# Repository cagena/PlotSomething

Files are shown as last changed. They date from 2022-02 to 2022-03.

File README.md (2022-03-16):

# PlotSomething

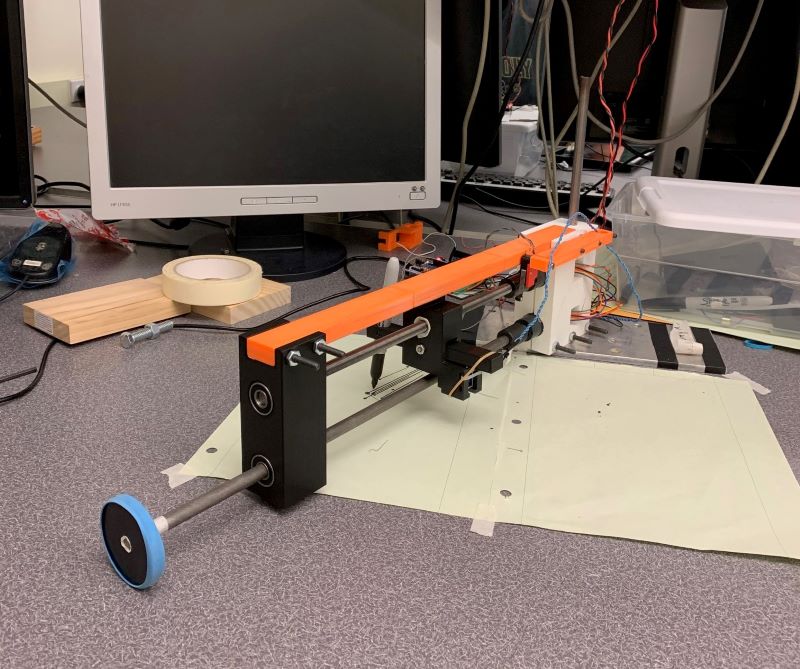
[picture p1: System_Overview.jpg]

Figure 1. System Overview

## Introduction

Our device is a pen plotter system that automatically plots an image through the use of an hpgl file. Through a serial terminal window, 
the user is initially prompted to calibrate the pen. Next, the user presses ‘p’ to plot, ‘q’ to quit, and ‘h’ to return to the welcome screen. 
After pressing ‘p’ to plot, the user is prompted to enter a hpgl filename. Once that is completed, the device will start to read the hpgl file 
and plot as the program reads each coordinate. If this filename doesn’t exist in the folder, it will prompt a message that says, 
“invalid file name”. This device is meant for people who are able to convert their desired image into an hpgl file and for those 
who want to plot something on paper without having to draw it themselves. This device is also for people who don’t want a typical, 
boring printed image on a piece of paper.

## Hardware Overview

The following table displays all of our hardware components used in this project. Fasteners such as screws, bolts, and nuts are not listed.

| Part No.  | Part |  Qty. | Source |
|:---:|:---|:-----:|:---|
| 1 | 2-in Drive Wheel | 1 | 3-D Printed |
| 2 | Track Slider/Solenoid Carrier | 1 | 3-D Printed |
| 3 | Lever Arm/Pen Carrier | 1 | 3-D Printed |
| 4 | Motor Mount | 1 | 3-D Printed |
| 5 | T-Slot Framing Rail | 1 | 3-D Printed | 
| 6 | Drive Shaft and Lead Screw Mount  | 1 | 3-D Printed |
| 7 | Limit Switch Mount | 1 | 3-D Printed | 
| 8 | Metal Base Plate | 1 | ME405 Lab |
| 9 | Base Shaft | 1 | ME405 Lab |
| 9 | 3/8 in Drive Shaft | 1 | Home Depot |
| 10 | 3/8 in-24 Threaded Rod | 1 | McMasterCarr |
| 11 | 3/8 in-24 Hex Nut | 1 | Home Depot |
| 12 | DC Voltage Limit Switch | 1 | Amazon |
| 13 | Solenoid (5V, 1.1A) | 1 | Amazon |
| 14 | Roller Bearing | 5 | Amazon |
| 15 | Set Screw Shaft Coupling | 2 | McMasterCarr |
| 16 | Black FinePoint Sharpie&trade; | 1 | Campus Bookstore  |
| 17 | Rubber Band | 2 | Home |
| 18 | Nucleo with Shoe	 | 1 | ME405 Tub |
| 19 | Mini Breadboard	 | 1 | ME405 Tub |
| 20 | P40NF03L MOSFET	 | 1 | IEEE Campus Store |
| 21 | 1N4004 Diode	 | 1 | ME405 Lab |
| 22 | 5 Ohm Resistor | 1 | ME405 Lab |

Our pen plotter project uses a cylindrical axis system that has one axis of rotation at the base shaft:
- Theta: A drive shaft rotates using the torque from a motor connected to a drive wheel.
- Radial: A lead screw moves the pen radially using the torque from a second motor.

The vertical base shaft rotates about the center of axis of rotation by being press-fit into a roller bearing, 
which was press-fitted into a metal plate that sits on the tabletop.

We 3-D printed a mount to keep both motors stationed close to the base shaft. The two motors are connected 
to a drive shaft and a lead screw using set screw shaft couplings. Since the motors don’t have enough torque 
to drive the entire system, we created a larger torque by incorporating a drive wheel. This drive wheel was 
3-D printed, and a rubber band was wrapped around the diameter of the wheel to provide friction when it contacts 
the table. The drive wheel was press-fitted into the drive shaft, and masking tape was used to create a tighter fit. 

As the lead screw nut undergoes translational motion, we ensured that the lead screw did not rotate by incorporating a 
slider mechanism. Using a 3-D printed part that acts as a T-Slot framing rail, we 3-D printed a track slider to fit 
within the slot clearance. We designed this track slider to have the lead screw nut press-fitted inside, so as the lead 
screw rotates, the slider prevents any rotation around the lead screw. We used masking tape to ensure a tighter 
press-fit. See figure 2 below for reference.

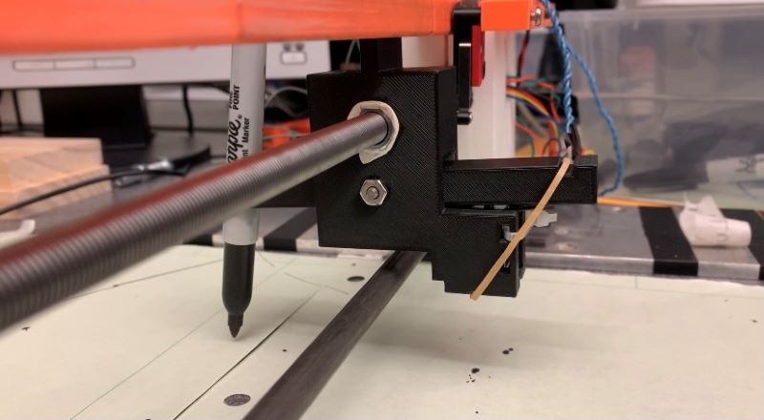
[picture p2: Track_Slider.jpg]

Figure 2. Close-Up Shot of Track Slider and Lever Arm

The right side of the track slider part has a holder that secures the solenoid using a light press-fit and a zip tie. 
As seen in the figure above, the track slider has a lever arm mechanism attached to it. For our system, we incorporated 
a lever arm that holds the sharpie. We used a spacer, screw, washer, and nut to attach the lever arm to the center of 
the track slider, allowing the lever arm to rotate about the same axis as the lead screw. Once the solenoid is actuated, 
the solenoid will extend and hit the lever arm, causing the sharpie to slightly rotate along with the level arm. When 
the solenoid is not extended, the lever arm rotates back to its original horizontal position by use of the rubber band, 
which acts as a spring. This is how we controlled whether or not the pen stayed in contact with the paper. For hardware
parts used to set up our solenoid, we followed a circuit diagram provided by Dr. Ridgeley, as shown below.

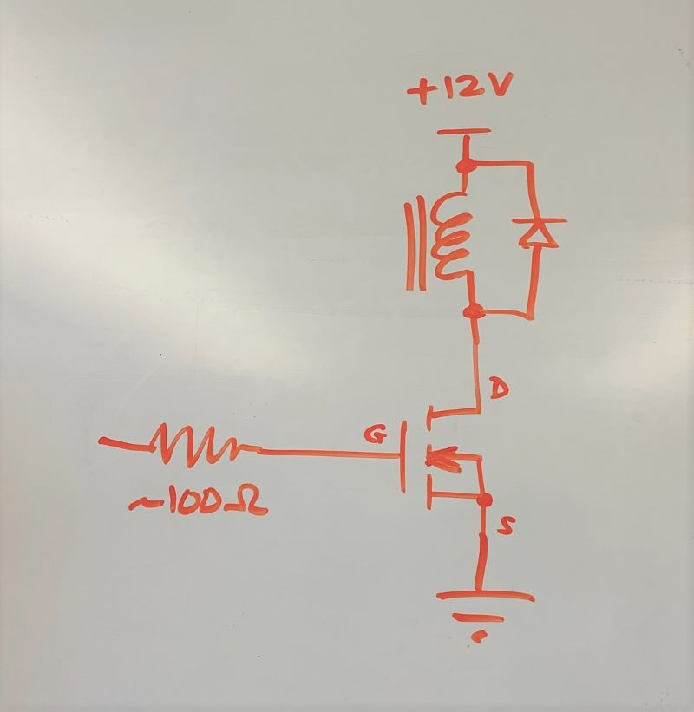
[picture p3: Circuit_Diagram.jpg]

Figure 3. Circuit Diagram

The figure above shows a supply voltage of 12 volts, but our solenoid was rated for 5 volts, so we used the lab's power supply 
to provide 5 volts instead of 12 volts. In addition, we used a 5 ohm resistor instead of a 100 ohm resistor.

The picture below shows our implementation of the circuit diagram using a MOSFET, resistor, diode, and wires connected 
to the solenoid and power supply.

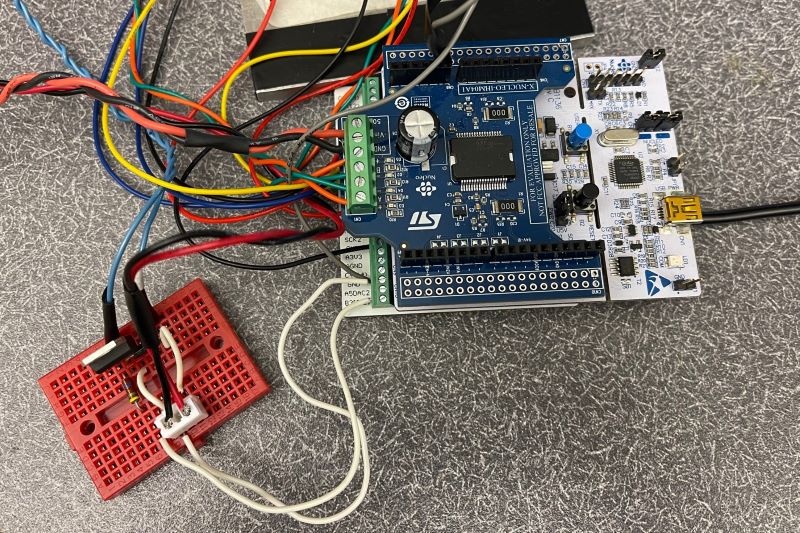
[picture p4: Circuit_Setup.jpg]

Figure 4. Circuit Setup

The final hardware component was a limit switch that was used to calibrate our system. The limit switch output was read with
a analog pin that allowed us to zero the encoders and identify when the pen reached the origin. We secured the limit switch
to the T-slot framing rail using screws and nuts and repurposing a previous iteration of our 3-D printed lever arm.

## Software Overview

As mentioned in the introduction, the software consists of a user interface that waits for user input to transition
between states. This user task is ran simultaneously with two motor tasks that continuosly sets the setpoint of the
controllers, sets the duty cycles of the motors, reads from the encoders, and runs the controllers themselves. The
tasks were added to a task manager run by the cotask file provided by Dr. Ridgely. The cotask file allows parallel
multitasking with the implementation of priorities so that some task will run before others. The
initial plan was to use queues to communicate the points from the hpgl file to the motor tasks and the controller.
However, the timing between each point became a concern. To solve this issue and to avoid issues that were caused
by the queues themselves a driver was created to read values from the hpgl output sequencially using a seperate
variable. Conceptually, this idea of running the controller and setting a flag to true when the encoder reading
was within the desired tolerance of the set point was possible. Then getting the next value from the driver would
be timed properly. Reflecting on it now, this design was used in an attempt to work around the queues that would
have provided this capability outright. The lasting issue was with the data allocation and handling the commands
in the form of characters rather than integers. If this project was continued queues would be implemented for the
communication between the motor tasks and the hpgl file that is read within the user task. The documentation for
the software can be accessed at the link below.

Software Documentation: https://cagena.github.io/PlotSomething/

## Results

We tested our system by creating an image and converting that to an hpgl file. From there, we found that our program couldn't properly read 
through all of the coordinates in the hpgl file. It read up to a certain coordinate and got stuck in our code somewhere. We ultimately 
ran out of time to debug, but we managed to get a curved line and straight line drawn on paper. Our system was successful in the sense that 
it was able to reach the first few coordinates, and the solenoid/pen/lever arm mechanism worked really well. The small solenoid was able to 
move the lever arm just enough for the pen to make contact with the paper. Our hardware seemed very robust, but we ran out of time to develop 
the software. The only downside of our hardware was the T-slot framing rail. We had to 3-D print this part last minute because the McMasterCarr 
part did not come in time. Most 3-D printers did not have a large enough print bed, so we had to split the rail into 3 sections and stick two rods 
through to connect all of them. This caused some raised edges, which did not provide enough clearance for the track slider to smoothly slide 
through on one of the sides. That affected our ability to properly calibrate the position of the pen, since it couldn't reach the limit switch.

If we could make some improvements to our system, we would use the aluminum T-slot framing rail from McMasterCarr or split up our 3-D printed framing 
rail into 3 sections in a different way (so that the track slider did not get caught near the base). Instead of having it split into 3 equal lengths, 
we would split it up so that the most important middle section was printed in one part, and the end sections were printed separately. In addition, we 
would figure out a way to implement a second limit switch for the rotation of the drive shaft and drive wheel. This way, we can calibrate our theta value 
to consistently plot from a selected origin every time our program ran. We would also try to figure out a different design that doesn't use the rubber 
band as a spring for our lever arm mechanism. If the rubber band is consistently used, the wear and tear of it will prevent the springing action we need 
to return the lever arm to a horizontal position.

We learned that focusing on hardware and software at the same time was very challenging, since one could not be fully tested without the other. 
The time constraint of this project ultimately caught up to us, especially since our McMasterCarr part did not come in time. In addition, we found it 
difficult to put the hardware together, since we did not have direct access to a 3-D printer. Fortunately, our friends were very kind and 
helped us 3-D print parts for this project. In addition, designing the hardware, especially the 3-D printed parts, was very challenging since we used 
press-fits, and it took up time re-designing parts when they did not fit properly. We also struggled figuring out the solenoid because our initial MOSFET 
selection was not working properly, so we spent a lot of time trying to figure out what was going wrong. In the end, we bought a new MOSFET that was 
fitting for our use, and it worked well with our solenoid. 

Although it was a really challenging project, we learned a lot about hardware (fasteners, press fits), electronics (MOSFETs, solenoids, limit switches), and
coding (hpgl files, code pertaining to solenoids and limit switches). We also learned how to quickly adapt and handle issues as they came up. Overall, this 
project was a really valuable learning experience.

## Additional Links
CAD Files: https://github.com/cagena/PlotSomething/tree/main/SolidWorks

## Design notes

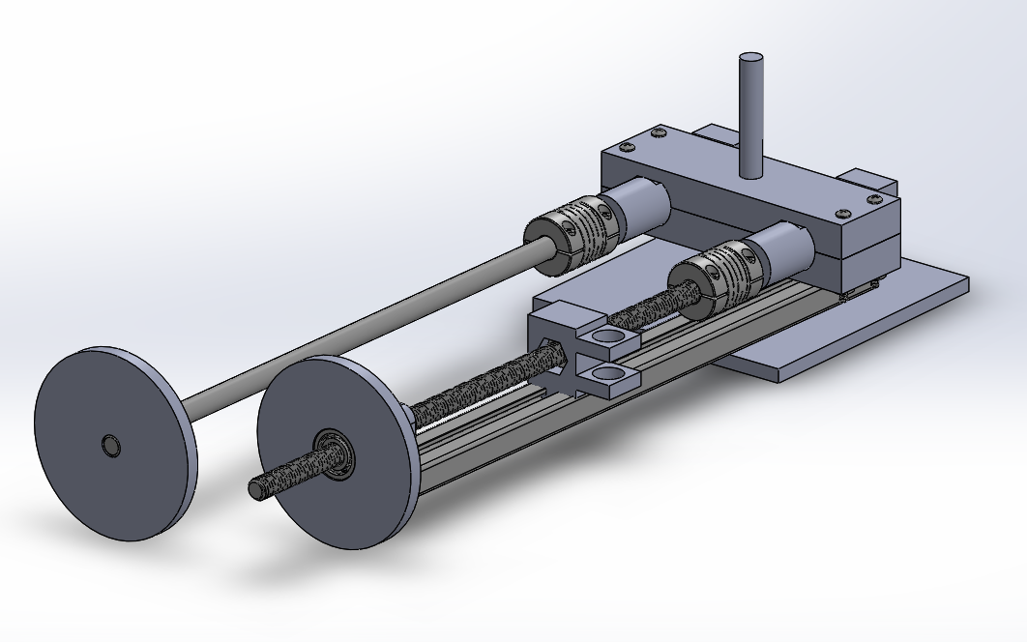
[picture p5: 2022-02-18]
Project Proposal/Fixture_1.png

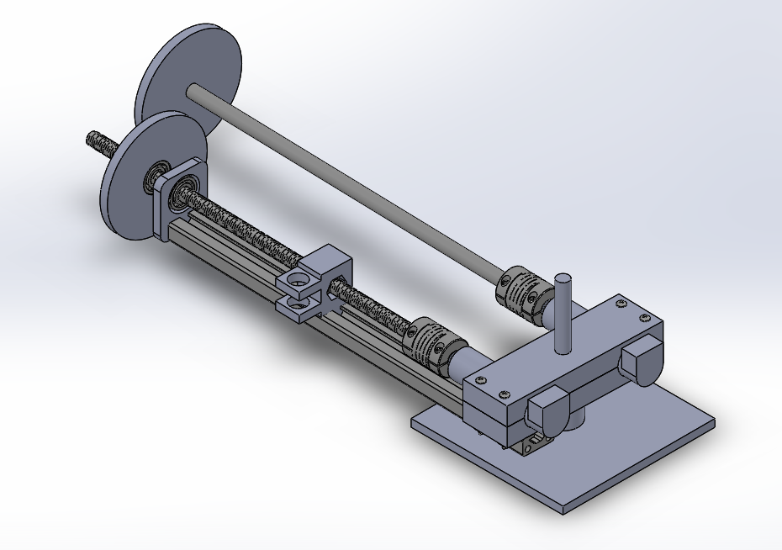
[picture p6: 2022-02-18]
Project Proposal/Fixture_2.png

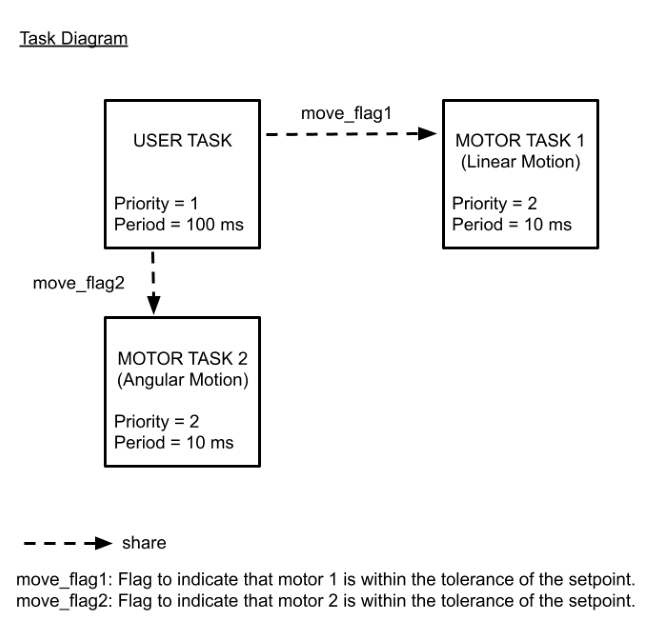
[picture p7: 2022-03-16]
docs/Task_Diagram.png

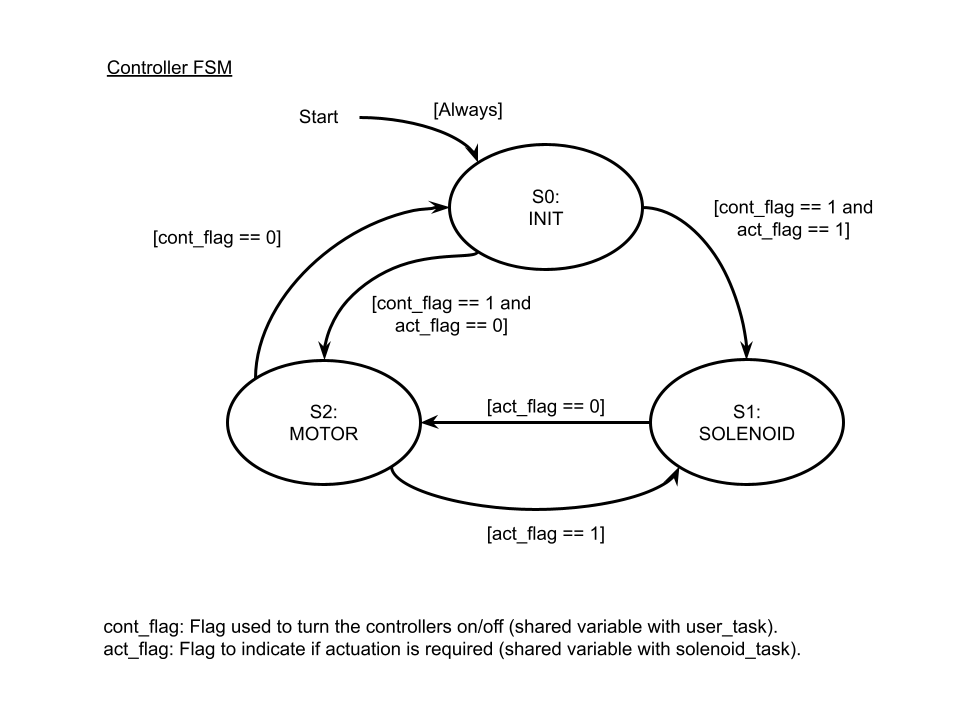
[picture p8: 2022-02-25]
docs/Controller_FSM.png

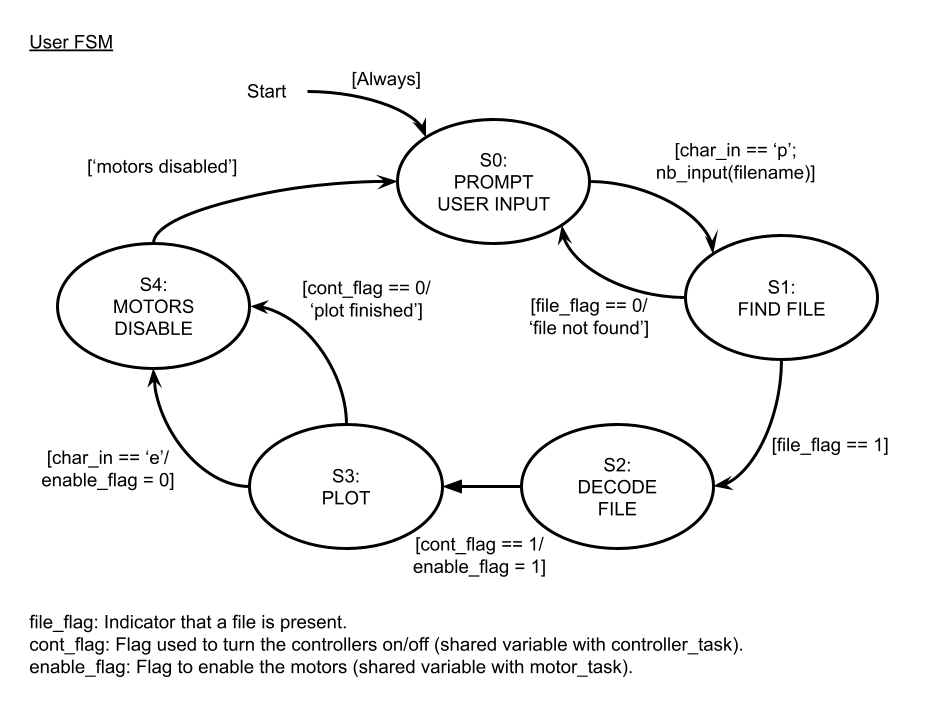
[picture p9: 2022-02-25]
docs/User_FSM.png

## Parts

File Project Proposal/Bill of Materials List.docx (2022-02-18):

- Lead screw & nuts
- Solenoid
- Slider bars (track)
- Drive shaft & coupling
- Wheels
- Bearings
- Screws for mounting motors
- Mount for motors (3D printed)
- Platform

Solenoid from Digikey:

https://www.digikey.com/en/products/detail/sparkfun-electronics/ROB-11015/6163694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

Inspiration/Ideas:

https://www.vxb.com/Black-Anodized-Aluminum-V-Slot-Extrusion-Profile-p/Anodized-Plate-Set-1000mm-Rail.htm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

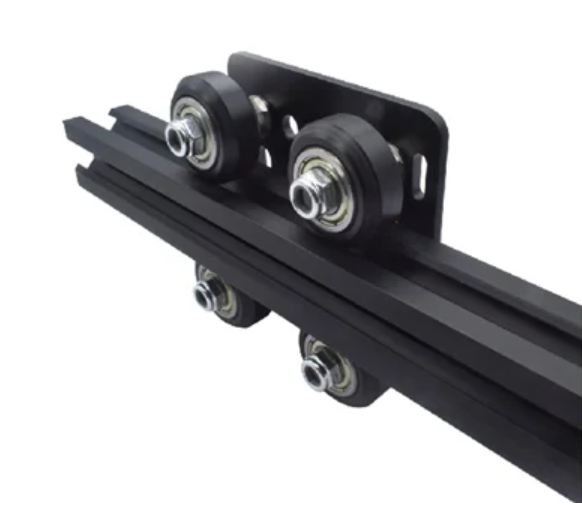
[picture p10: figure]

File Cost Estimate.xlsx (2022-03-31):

What is it for? | Brand | Part Name | Vendor | # of Units in Package | # of Units to Purchase | Total Price | Obtained Yet? | URL
Lead Screw Nut | Everbilt | #3/8-24 Zinc Plated Machine Screw Nut | Home Depot | 4 | 2 | $2.56 | Y | https://www.homedepot.com/p/Everbilt-10-24-Stainless-Steel-Machine-Screw-Nut-4-Pack-800031/204274134
Lead Screw | Everbilt | 3/8 in.-24 x 12 in. Low Strength Steel Threaded Rod | McMasterCarr | 1 | 1 | $1.09 | Y | https://www.mcmaster.com/catalog/128/3476
Motor Mount Screw |  | #10-24 x 1-1/2 in Machine Screw
Motor Mount Nut |  | #10-24 x 1-1/2 in Nut
Drive Shaft |  | 3/8 in. x 36 in Drive Shaft | Home Depot | 1 | 1 | $5.98 | Y | https://www.homedepot.com/p/3-8-in-x-36-in-Plain-Steel-Round-Rod-802447/204273959
Base Shaft |  | 3/8 in. Base Shaft
Shaft Coupling |  | Set Screw Shaft Coupling, Black-Oxide Steel, for 3/8" Diameter Round Shaft | McMasterCarr | 1 | 2 | $25.24 | Y | https://www.mcmaster.com/shaft-couplings/set-screw-shaft-couplings/
Shaft/Lead Screw Bearings |  | 3/8 in. Bearings for Screw and Shaft | Amazon | 10 | 1 | $12.99 | Y | https://www.amazon.com/Donepart-R6-2RS-Bearings-Pre-Lubricated-Double/dp/B07X93RV9L?s=industrial
T-Track Slider |  | Aluminum T-slider Track (length: 16 in) | McMasterCarr | 1 | 1 | $3.84 | N | https://www.mcmaster.com/6575N215/
Solenoid |  | Solenoid | Amazon | 1 | 1 | $11.95 | Y | https://www.amazon.com/gp/product/B0722JK1L1/ref=ox_sc_act_title_1?smid=A1283MCABFXB0Q&psc=1
Driving Wheel |  | Wheel
Limit Switch |  | Limit Switch | Amazon |  | 1 |  | N
NOTES:
Green text means parts found in ME 405 Lab
Alternatives if parts don't work out:
Motor Mount Screw |  | #10-24 x 1-1/2 in Machine Screw | McMasterCarr | 5 | 2 | $2.56 | N | https://www.homedepot.com/p/10-24-x-1-1-2-in-Combo-Round-Head-Zinc-Plated-Machine-Screw-5-Pack-803221/204274627
Motor Mount Nut |  | #10-24 x 1-1/2 in Nut | Home Depot |  |  |  | N
Base Shaft |  | 3/8 in. Base Shaft |  |  |  |  | N
Items Bought
Purchaser | Vendor | Items | Price | Price Split in Half:
Corey | Amazon | Bearings, Solenoid | $27.13 | $13.56
Luisa | McMasterCarr | Shaft Couplings, Threaded Rod (Lead Screw) | $37.79 | $18.89
Luisa | Home Depot | 36 in Metal Rod, 6 X 3/8-in nuts | $7.55 | $3.77
 |  |  | Luisa Total: | $22.67
 |  |  | Corey Total: | $13.56
 |  |  | Difference: | $9.10

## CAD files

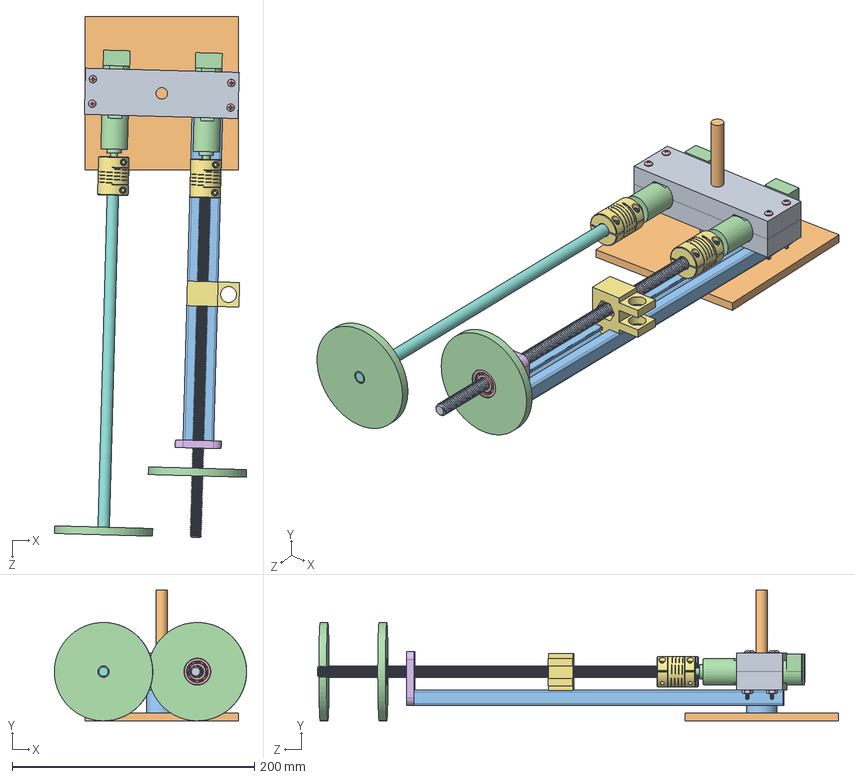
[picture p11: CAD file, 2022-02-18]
Project Proposal/SolidWorks/Plotter.SLDASM
158.9 x 108.0 x 430.4 mm
Motor Mount x 2
Base
Spacer
Motor x 2
Phillips Screw x 4
0.125 Hex Nut x 4
Flexible Shaft Coupling x 2
Rotary Shaft
Threaded Rod
.375 Hex Nut
T-Slotted Framing Rail
Our Wheel x 2
Permanently Lubricated Ball Bearing x 2
Part2^Plotter
Pencil Holder

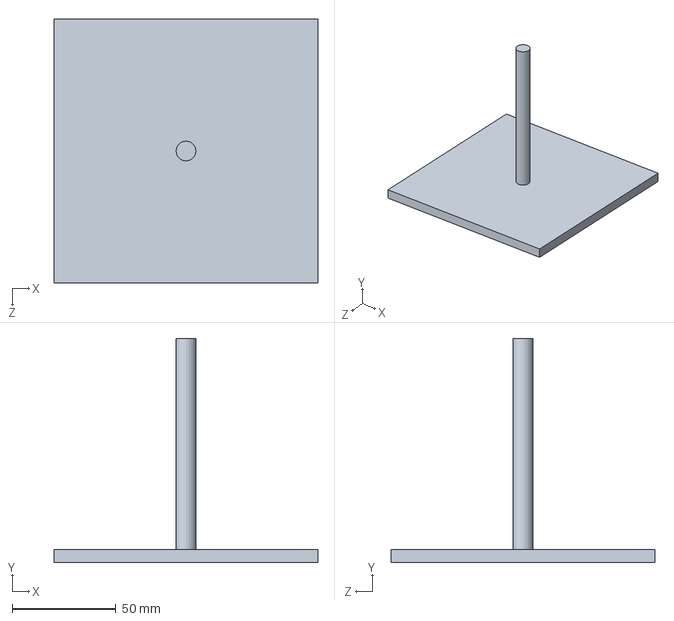
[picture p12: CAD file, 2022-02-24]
SolidWorks/Plotter_v2.SLDASM
127.0 x 108.0 x 127.0 mm

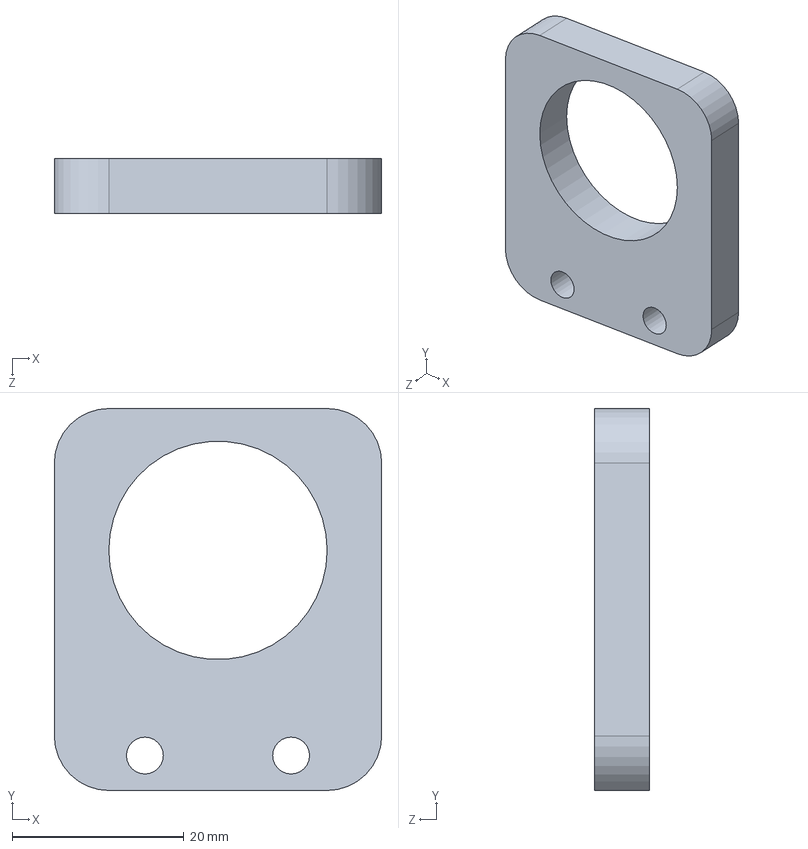
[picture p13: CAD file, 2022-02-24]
Project Proposal/SolidWorks/Attachment.SLDPRT
38.1 x 44.5 x 6.35 mm

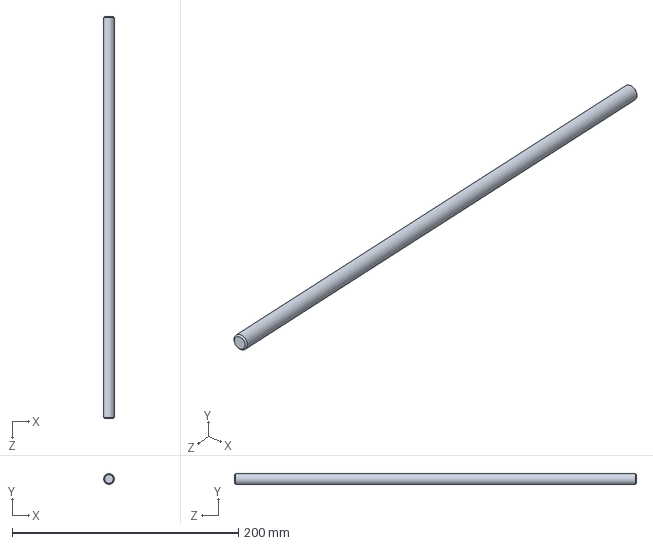
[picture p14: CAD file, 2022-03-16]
SolidWorks/Rotary Shaft.SLDPRT
9.53 x 9.53 x 355.6 mm

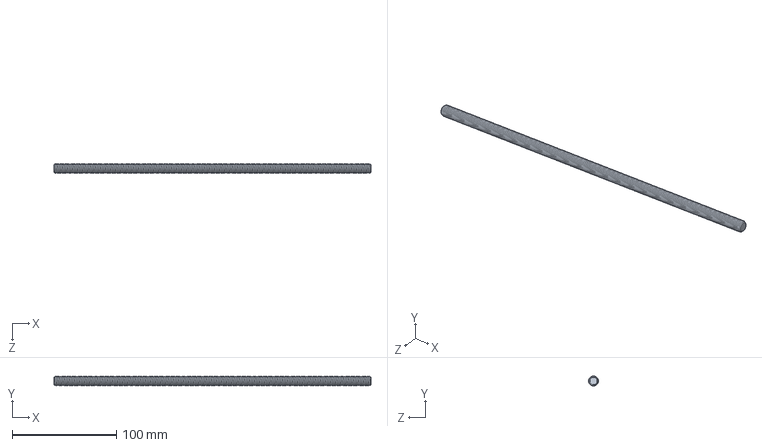
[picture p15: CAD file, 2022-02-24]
Project Proposal/SolidWorks/Threaded Rod.SLDPRT
304.8 x 9.53 x 9.53 mm

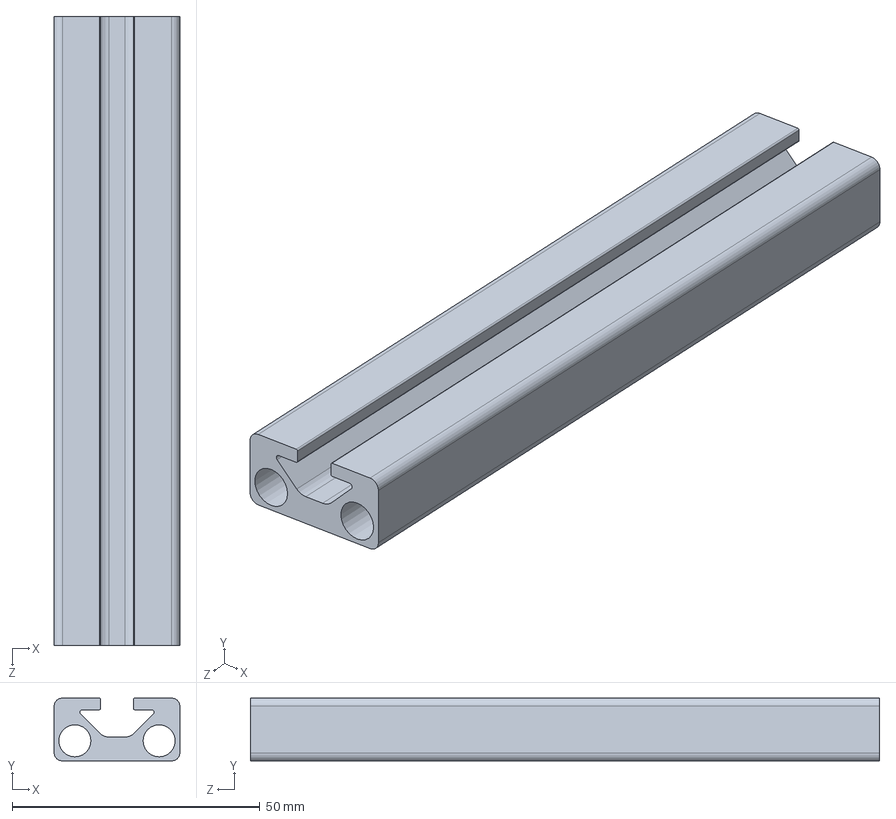
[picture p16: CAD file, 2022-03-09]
SolidWorks/T-Slotted Framing Rail Middle.SLDPRT
25.4 x 12.7 x 127.0 mm

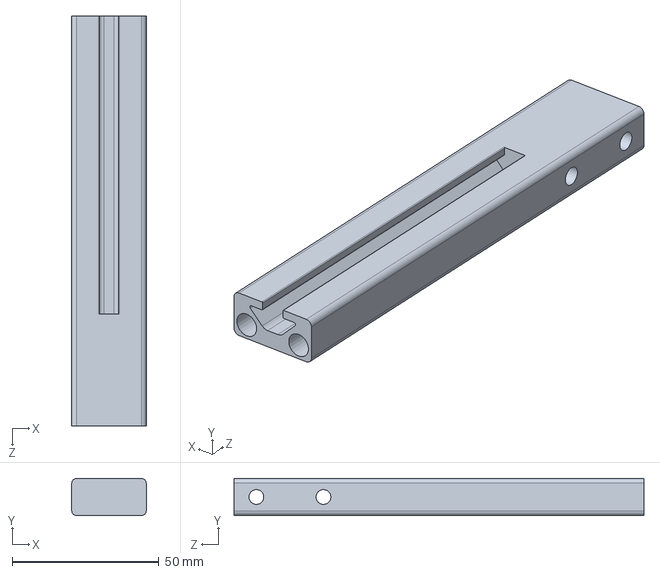
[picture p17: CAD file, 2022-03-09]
SolidWorks/T-Slotted Framing Rail Wheel Side.SLDPRT
25.4 x 12.7 x 139.7 mm

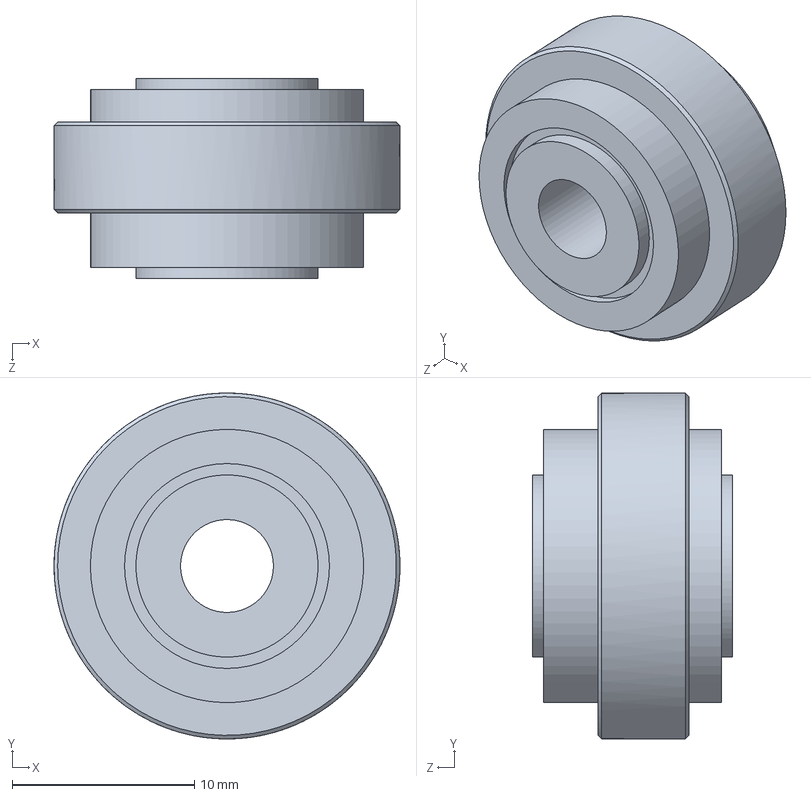
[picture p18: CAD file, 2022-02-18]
Project Proposal/SolidWorks/Small Wheel.SLDPRT
19.0 x 19.0 x 11.0 mm

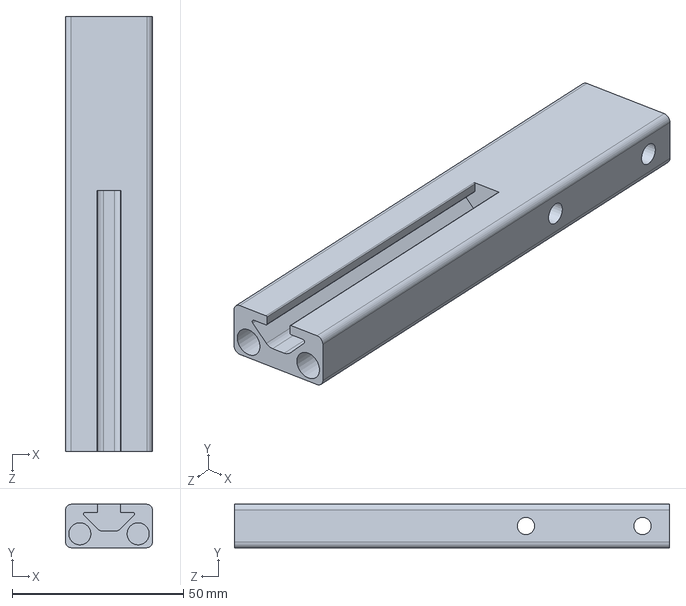
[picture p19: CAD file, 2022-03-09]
SolidWorks/T-Slotted Framing Rail Motor Side.SLDPRT
25.4 x 12.7 x 127.0 mm

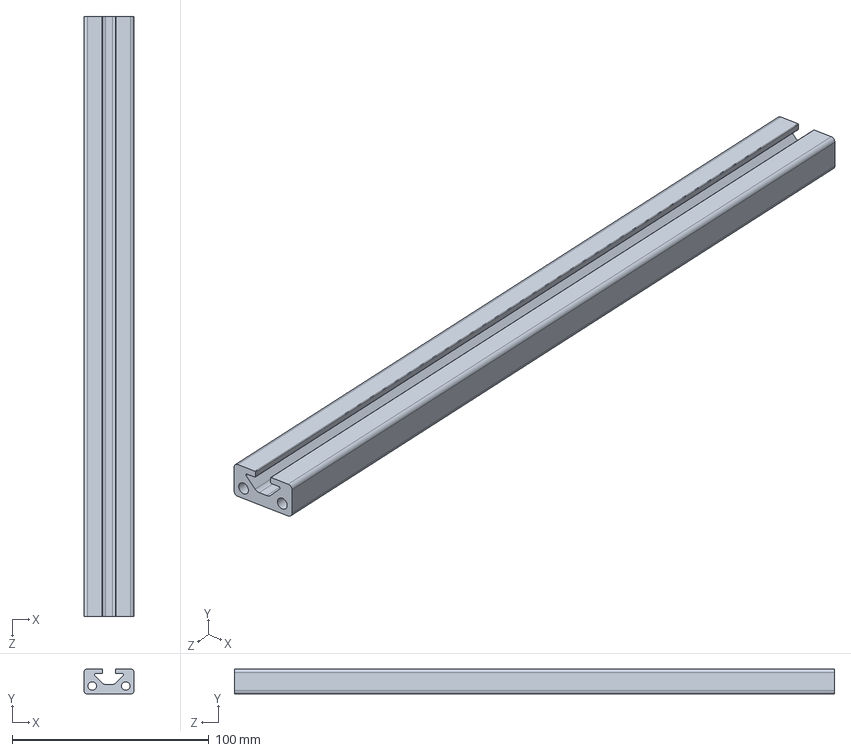
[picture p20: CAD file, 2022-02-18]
Project Proposal/SolidWorks/T-Slotted Framing Rail.SLDPRT
25.4 x 12.7 x 304.8 mm

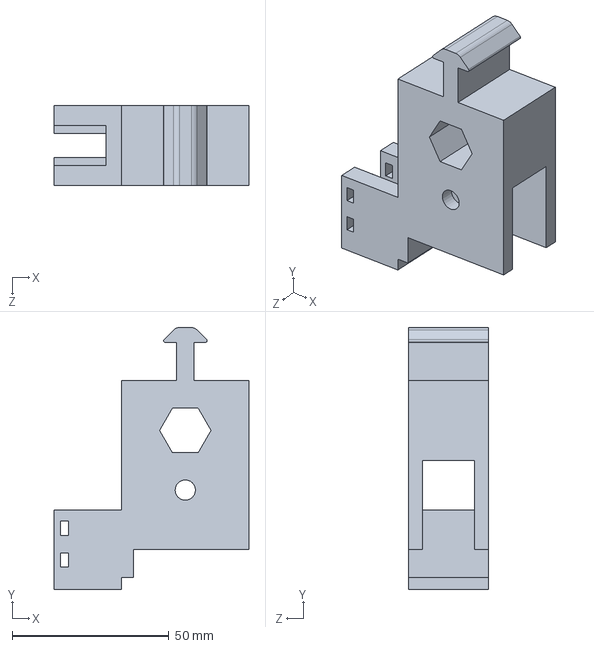
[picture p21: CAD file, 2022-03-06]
SolidWorks/TrackSliderv6.SLDPRT
62.2 x 83.7 x 25.4 mm

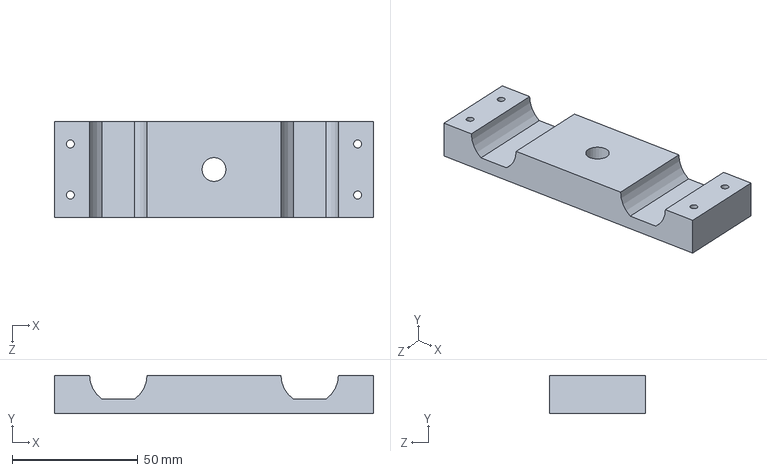
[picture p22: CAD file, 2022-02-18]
Project Proposal/SolidWorks/Motor Mount.SLDPRT
127.0 x 15.2 x 38.1 mm

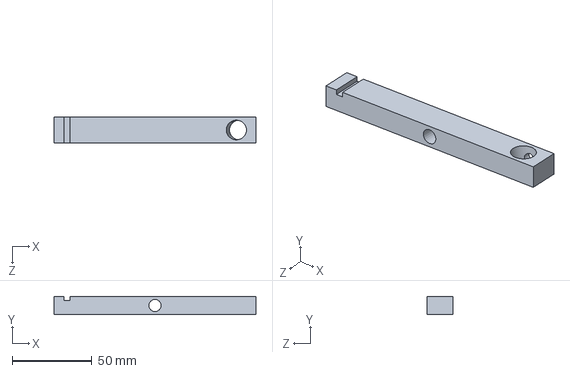
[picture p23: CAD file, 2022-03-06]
SolidWorks/Seesaw_v2.SLDPRT
127.0 x 11.4 x 16.3 mm

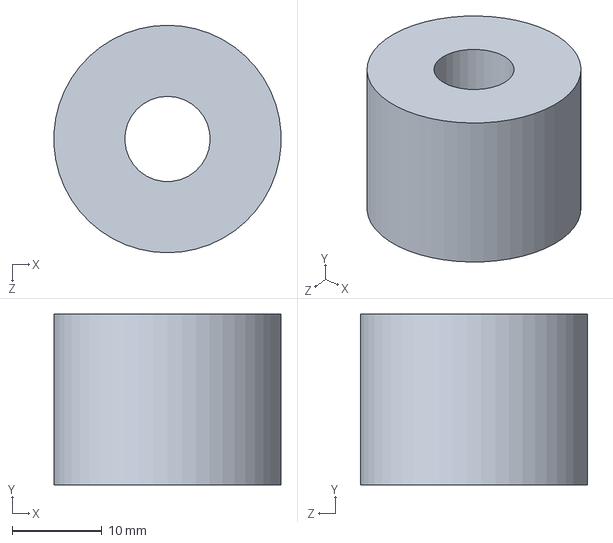
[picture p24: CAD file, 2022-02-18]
Project Proposal/SolidWorks/Spacer.SLDPRT
25.3 x 19.1 x 25.4 mm

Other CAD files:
SolidWorks/TrackSliderv4.SLDPRT
Project Proposal/SolidWorks/Motor.SLDPRT
SolidWorks/TrackSliderv5.SLDPRT
Project Proposal/SolidWorks/Permanently Lubricated Ball Bearing.SLDPRT
Project Proposal/SolidWorks/.375 Hex Nut.SLDPRT
Project Proposal/SolidWorks/0.125 Hex Nut.SLDPRT
Project Proposal/SolidWorks/Base.SLDPRT
Project Proposal/SolidWorks/Flexible Shaft Coupling.SLDPRT
Project Proposal/SolidWorks/Medium Wheel.SLDPRT
Project Proposal/SolidWorks/Mount.SLDPRT
Project Proposal/SolidWorks/Our Wheel.SLDPRT
Project Proposal/SolidWorks/Pencil Holder.SLDPRT
Project Proposal/SolidWorks/Phillips Screw.SLDPRT
Project Proposal/SolidWorks/Rotary Shaft.SLDPRT
Project Proposal/SolidWorks/T-Slotted Framing.SLDPRT
Project Proposal/SolidWorks/Wheel.SLDPRT
SolidWorks/#10 Phillips Screw.SLDPRT
SolidWorks/#10 Steel Hex Nut.SLDPRT
SolidWorks/.375 Steel Hex Nut.SLDPRT
SolidWorks/Base.SLDPRT
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

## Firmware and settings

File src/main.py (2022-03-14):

"""!
@file main.py
This is the main file for Lab 3, it contains a program that runs two motor tasks which includes closed loop control
for each motor. The code was adapted from Dr. Ridgely's basic task example.
@author Corey Agena
@author Luisa Chiu
@date 2-9-2022
"""

# Import the required modules.
import gc
import pyb
import cotask
import encoder_agena_chiu
import motor_agena_chiu
import controller_agena_chiu
import task_share
from pyb import USB_VCP
from nb_input import NB_Input
from micropython import const
import hpgl_agena_chiu
import sys

## State 0 of the user interface task
S0_CALIB            = const(0)
## State 1 of the user interface task
S1_HELP             = const(1)
## State 2 of the user interface task
S2_WAIT_FOR_CHAR    = const(2)
## State 3 of the user interface task
S3_READ             = const(3)
## State 4 of the user interface task
S4_PLOT             = const(4)

## Variable representing the input to the serial port.
nb_in = NB_Input (USB_VCP(), echo=True)   

def task_motor1(duty_cycle = 0):
    '''!
    Task which runs the motor, encoder, and controller drivers to 
    control the duty cycle for motor 1.
    @param duty_cycle The initial cycle of motor 1.
    '''
    while True:
        ## A variable that holds the position of encoder 1.
        enc1 = -encoder_drv1.read()
        ## A variable that defines duty cycle for the run funciton of controller 1.
        duty_cycle = controller_1.run(enc1, 100)
        motor_drv1.set_duty_cycle(duty_cycle)
        ## A flag that indicates that motor 1 reached the desired setpoint within the set limits.
        flag1 = controller_1.flag()
        if flag1 == True:
            move_flag1.put(1)
            flag1 = False
        yield()

def task_motor2(duty_cycle = 0):
    '''!  
    Task which runs the motor, encoder, and controller drivers to 
    control the duty cycle for motor 2.
    @param duty_cycle The initial cycle of motor 2.
    '''
    while True:
        ## A variable that holds the position of encoder 2.
        enc2 = -encoder_drv2.read()
        ## A variable that defines duty cycle for the run funciton of controller 2.
        duty_cycle = controller_2.run(enc2,75)
        motor_drv2.set_duty_cycle(-duty_cycle)
        ## A flag that indicates that motor 2 reached the desired setpoint within the set limits.
        flag2 = controller_2.flag()
        if flag2 == True:
            move_flag2.put(1)
            flag2 = False
        yield()
        
def input_task():
    '''! 
    Task which runs the non-blocking input object quickly to ensure
    that keypresses are handled not long after they've occurred.
    '''
    while True:
        nb_in.check ()
        yield ()

def task_user(state = S0_CALIB):
    '''!  
    Task which includes multiple states that guide the user through the
    use of the pen plotter system. This includes: calibration, help, read, and
    plot states.
    @param state The initial state of the user task.
    '''
    while True:
        if state == S0_CALIB:
            sol.low()
            print('\r\nReady to Calibrate? Press c and Enter')
            if nb_in.any ():
                ## Variable for the character read from the serial port.
                char_in = nb_in.get()
                if char_in == 'c':
                    print('\r\nCalibrating')
                    ## Pin variable for the limit switch.
                    pin = pyb.Pin(pyb.Pin.cpu.A0, pyb.Pin.IN)
                    ## ADC variable for the pin above.
                    adc = pyb.ADC(pin)
                    ## Value read from the ADC.
                    val = adc.read()
                    if val > 10:
                        motor_drv1.set_duty_cycle(-100)
                        while True:
                            val = adc.read()
                            if val <= 5:
                                encoder_drv1.zero()
                                encoder_drv2.zero()
                                motor_drv1.set_duty_cycle(0)
                                state = S1_HELP
                                break
                    else:
                        encoder_drv1.zero()
                        encoder_drv2.zero()
                        motor_drv1.set_duty_cycle(0)
                        state = S1_HELP
                        
        elif state == S1_HELP:
            print('\n\rWelcome, press:'
                  '\n\'p\' to plot from a HPGL file'
                  # '\n\'l\' to prompt the user to enter a setpoint for'
                  # ' lead screw'
                  '\n\'q\' to quit'
                  '\n\'h\' return to the welcome screen')
            state = S2_WAIT_FOR_CHAR
            
        elif state == S2_WAIT_FOR_CHAR:
            if nb_in.any ():
                ## Variable for the character read from the serial port.
                char_in = nb_in.get()
                if char_in == 'q':
                    motor_drv1.set_duty_cycle(0)
                    motor_drv2.set_duty_cycle(0)
                    print('\r\nThe program was exited')
                    sys.exit()
                elif char_in == 'h':
                    state = S1_HELP
                    print('\r\n')
                # elif char_in == 'l':
                #     print('\r\nLinear position adjustment')
                #     if nb_in.any():
                #         char_in = nb_in.get()
                #         if char_in == '+':
                #             print('\r\nPositve Linear Motion')
                #             motor_drv1.set_duty_cycle(100)
                #         elif char_in == '-':
                #             print('\r\nNegative Linear Motion')
                #             motor_drv1.set_duty_cycle(-100)
                #         elif char_in == 's':
                #             print('\r\nStopped Motion')
                #             motor_drv1.set_duty_cycle(0)
                elif char_in == 'p' or char_in == 'P':
                    state = S3_READ
                    i = 0
        
        elif state == S3_READ:
            if i == 0:
                print('\r\nEnter hpgl file name:')
            elif nb_in.any ():
                ## Variable holding the file name to be read.
                filename = nb_in.get()
                print('\r\n',filename)
                if '.hpgl' in filename or '.HPGL' in filename:
                    hpgl.read(filename)
                    state = S4_PLOT
                    ## Counter for the amount of times ran through the plot state.
                    plot_count = 0
                    move_flag1.put(1)
                    move_flag2.put(1)
                    print('Plotting')
                else:
                    print('\r\ninvalid file name')
            i += 1
        
        elif state == S4_PLOT:
            mflag1 = move_flag1.get()
            mflag2 = move_flag2.get()
            if mflag1 and mflag2:
                print('in loop')
                move_flag1.put(0)
                move_flag2.put(0)
                hpgl.process(plot_count)
                ## The ouptut from hpgl.run()
                output = hpgl.run(plot_count)
                ## The command or number in the 0 position of the output list.
                x = output[0]
                try:
                    float(x)
                except:
                    if x == 'PU':
                        print('ho')
                        sol.low()
                        plot_count += 1
                        move_flag1.put(1)
                        move_flag2.put(1)
                    elif x == 'PD':
                        print('he')
                        sol.high()
                        plot_count += 1
                        move_flag1.put(1)
                        move_flag2.put(1)
                    elif x == 'IN' and plot_count > 0:
                        print('Done')
                        state = S1_HELP
                    else:
                        print('hi')
                        move_flag1.put(1)
                        move_flag2.put(1)
                        plot_count += 1
                else:
                    print('uh')
                    if output[1]:
                        print('uhh')
                        ## The number in the second position of the output list.
                        y = output[1]
                        controller_1.set_setpoint(x)
                        controller_2.set_setpoint(y)
                        plot_count += 1
        yield ()

# This code creates driver and task objects required for the pen ploter.
# It also runs a task scheduler that allows multitasking.
if __name__ == "__main__":
    ## A variable that creates a encoder driver for encoder 1.
    encoder_drv1 = encoder_agena_chiu.EncoderDriver(pyb.Pin.cpu.B6, pyb.Pin.cpu.B7, 4)
    ## A variable that creates a encoder driver for encoder 2.
    encoder_drv2 = encoder_agena_chiu.EncoderDriver(pyb.Pin.cpu.C6, pyb.Pin.cpu.C7, 8)
    ## A variable that creates a motor driver for motor 1.
    motor_drv1 = motor_agena_chiu.MotorDriver(pyb.Pin.cpu.A10, pyb.Pin.cpu.B4, pyb.Pin.cpu.B5, 3)
    ## A variable that creates a motor driver for motor 2.
    motor_drv2 = motor_agena_chiu.MotorDriver(pyb.Pin.cpu.C1, pyb.Pin.cpu.A0, pyb.Pin.cpu.A1, 5)
    ## A variable that creates a controller driver for motor 1.
    controller_1 = controller_agena_chiu.ControllerDriver(0, 0)
    ## A variable that creates a controller driver for motor 2.
    controller_2 = controller_agena_chiu.ControllerDriver(0, 0)
    # Enable both motors.
    motor_drv1.enable()
    motor_drv2.enable()
    
    ## A variable that creates a hpgl driver to read the hpgl file.
    hpgl = hpgl_agena_chiu.hpglDriver()
    
    ## A shared variable that indicates that motor 1 arrived at the desired position.
    move_flag1 = task_share.Share('B', name = 'Movement Flag 1')
    ## A shared variable that indicates that motor 2 arrived at the desired position.
    move_flag2 = task_share.Share('B', name = 'Movement Flag 2')
    
    sol = pyb.Pin(pyb.Pin.cpu.B3, pyb.Pin.OUT_PP)
    
    # Run the memory garbage collector to ensure memory is as defragmented as
    # possible before the real-time scheduler is started
    gc.collect ()
    
    # Set the controller gains and initial setpoints for both motors.
    controller_1.set_gain(0.1)
    controller_1.set_setpoint(0)
    controller_2.set_gain(0.1)
    controller_2.set_setpoint(0)
    
    # Set both encoders to zero.
    encoder_drv1.zero()
    encoder_drv2.zero()
    
    # Create the tasks. If trace is enabled for any task, memory will be
    # allocated for state transition tracing, and the application will run out
    # of memory after a while and quit. Therefore, use tracing only for 
    # debugging and set trace to False when it's not needed
    task1 = cotask.Task (task_motor1, name = 'Task_Motor1', priority = 2, 
                         period = 10, profile = True, trace = False)
    task2 = cotask.Task (task_motor2, name = 'Task_Motor2', priority = 2, 
                         period = 10, profile = True, trace = False)
    in_task = cotask.Task (input_task, name = 'Input Task', priority = 1, 
                           period = 50, profile = True, trace = False)
    task_user = cotask.Task (task_user, name = 'User Task', priority = 0, 
                           period = 100, profile = True, trace = False)
    cotask.task_list.append (task1)
    cotask.task_list.append (task2)
    cotask.task_list.append (in_task)
    cotask.task_list.append (task_user)
    while True:
        # Run the scheduler with the chosen scheduling algorithm. 
        cotask.task_list.pri_sched ()
    

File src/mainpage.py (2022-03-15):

"""!
@file mainpage.py
File that holds the main page.
@mainpage
@section intro Introduction
The term project is to design and build a 2.5 degree of freedom pen plotter.
The plotter was designed, built, and codedwithin a 3 week period. The code will
be explained here.

@section software Software Design
Throughout the quarter, software was developed for motion control,
multitasking, and program organization.There are 8 distinct .py files used for
the control of the pen plotter. The main.py file consists of the different
task generators and a main function portion. The tasks include two motor tasks,
a user task, and a input task. The main program initializes the drivers and 
runs the task manager that allows multitasking. The drivers operate hardware
including the motor and encoder; and also do some stand alone processing in
the form of a closed loop controller and hpgl file reader. More detail on the
driver files can be found at motor_agena_chiu.py, encoder_agena_chiu.py,
controller_agena_chiu.py, and hpgl_agena_chiu.py. The final three files were
provided by Dr. Ridgely. They are the cotask.py, task_share.py, and
nb_input.py. The cotask file allows for multitasking, the task share file
allows the use of shares and queues across tasks, and the nb_input allows the
reading of the serial port using non-blocking methods. The software was 
outlined in the form of a task diagram and multiple state transition
diagrams shown below.

@subsection task Task Diagram
The task diagram below shows how the tasks were implemented with the use of a
single share. The rest of the communication was completed using drivers. There
was a bug in the communication, that can be solved with the implementation of
a queue for each motor. Data allocation errors were apparent and an issue with
adding non-integer values caused attempt at different methods. After reworking
this task diagram it is apparent that in the attempt to fix the errors and
simplify the code the functionality and required components were lost. This
means that with some extra time, work, and the implementation of queues the
final bug could be resolved.
\image html Task_Diagram.png

@subsection user User Task
The user task is run on the microcontroller and it leads the user through the
proper use of the pen plotter. It starts with calibration, moving the pen to
its zero point along the radial direction. Then it prints the help screen with
the different commands that can be input to the serial port. Depending on the
command the help window will be printed again, the entire program will quit, 
or it will continue to the read state. The read state is where the hpgl file
is opened and read from using the hpgl driver. Once the file is found and 
read from then the program transitions to the plot state. This is where the
pen plotter is controlled toward the positions read from the hpgl file. The 
current software structure runs one location at a time, requiring a counter
input into the driver to keep track of which position has already been sent to
the plotter.
\image html User_FSM.png

@subsection motor Motor Task
The motor task has been simplified greatly. It handles the actuation of the
motors, reading from the encoders, and controlling the motors with a closed
loop controller. However, all of this continuously happens and does not
require input until a new setpoint is provided. So there are two states: set
duty and control. The finite state machine starts at set duty if the duty is
not changed then it is considered 0 and the motors are not actuated. If a
setpoint is entered then a new duty cycle will be calculated as a result and
the motors will acuate. When this happens the program enters the control state 
where the controller will approach the setpoint and raise a flag when the
encoders read within the specified tolerances. When the flag is raised then
the program waits for another setpoint and duty cycle.
\image html Motor_FSM.png

@subsection other Other Features
Other features include the solenoid, limit switch, and hpgl driver. The
solenoid is connected to a analog pin that is initialized then set high or low.
Since the position is remembered a task is not required for this piece of
hardware. The limit switch was used in the calibration state of the user task,
where the motor is actuated until the limit switch is hit and sets that point
to zero. The limit switch is connected to a analog pin that is initialized and
read from using the pyb.adc module and stoping the motor when that value
decreased below a set value of 5. Finally the hpgl driver reads the file and
processes the information multiple times to get them in the proper units and
scaled to fit the geometry and mechanics of the physical system.

@author Corey Agena
@author Luisa Chiu
@date Winter 2022
"""

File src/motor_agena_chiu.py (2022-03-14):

'''!
@file motor_agena_chiu.py
This is the file that serves as a module to be imported in main. It creates a class for the motor driver
to run functions.
@author Corey Agena
@author Luisa Chiu
@date 1-26-2022
'''

# Import the required modules.
import pyb
    
class MotorDriver:  
    '''! 
    This class implements a motor driver for an ME405 kit. 
    '''
    def __init__(self, en_pin, in1pin, in2pin, timer):
        '''! 
        Creates a motor driver by initializing GPIO
        pins and turning the motor off for safety. 
        @param en_pin pin for enabling the motor.
        @param in1pin pin 1 to control the motor.
        @param in2pin pin 2 to control the motor.
        @param timer timer to use for motor channels.
        '''
        ## The pin variable for the enable pin on the Nucleo.
        self.EN = pyb.Pin(en_pin, mode = pyb.Pin.OUT_OD,
                          pull = pyb.Pin.PULL_UP)
        
        ## The timer variable for the motor.
        self.tim = pyb.Timer(timer, freq = 20000)
        
        ## A pin variable to recieve the duty cycles.
        self.pin1 = pyb.Pin(in1pin, pyb.Pin.OUT_PP)
        ## A pin variable to recieve the duty cycles.
        self.pin2 = pyb.Pin(in2pin, pyb.Pin.OUT_PP)
        
        ## The channel variable for channel 1 and pin1.
        self.ch1 = self.tim.channel(1, mode = pyb.Timer.PWM,
                                    pin = self.pin1)
        ## The channel variable for channel 2 and pin2.
        self.ch2 = self.tim.channel(2, mode = pyb.Timer.PWM,
                                    pin = self.pin2)
        
        # Turn the motor off for safety.
        self.pin1.low()
        self.pin2.low()
        
    def enable(self):
        '''!
        Enables the motor, allowing power to it.
        '''
        self.EN.high()
        
    def disable(self):
        '''!
        Disables the motor, preventing power to it.
        '''
        self.EN.low()
        
    def set_duty_cycle(self, duty):
        '''!
        This method sets the duty cycle to be sent
        to the motor to the given level. Positive values
        cause torque in one direction, negative values
        in the opposite direction.
        @param duty A signed integer holding the duty
               cycle of the voltage sent to the motor 
        '''
        if duty > 0:
            self.ch1.pulse_width_percent(duty)
            self.ch2.pulse_width_percent(0)
        elif duty < 0:
            self.ch1.pulse_width_percent(0)
            self.ch2.pulse_width_percent(-duty)  
        else:
            self.ch1.pulse_width_percent(0)
            self.ch2.pulse_width_percent(0) 

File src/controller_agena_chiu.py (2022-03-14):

'''!
@file controller_agena_chiu.py
This is the file that serves as a module to be imported in main. It creates a class for the controller
driver to run functions.
@author Corey Agena
@author Luisa Chiu
@date 1-27-2022
'''
    
class ControllerDriver:  
    '''! 
    This class implements a controller driver for a motor and flywheel rig. 
    '''
    def __init__(self, K_p, i_set):
        '''! 
        Creates a controller driver by initializing the gain
        and initial setpoint used in closed-loop control.
        @param K_p The initial proportional gain for the controller.
        @param i_set The initial setpoint for the controller.
        '''
        ## Proportional Gain
        self.K_p = float(K_p)
        
        ## Initial setpoint
        self.i_set = float(i_set)
        
    def run(self,pos,max_duty):
        '''!
        Called repeatedly to run the control algorithm.
        @param pos Current position of the encoder.
        @return duty Duty cycle to set the motor.
        '''
        ## Error, difference between the current position and initial setpoint.
        if pos < self.i_set:
            self.error = abs(pos - self.i_set)
        elif pos > self.i_set:
            self.error = abs(pos - self.i_set)*(-1)
        elif pos == self.i_set:
            self.error = 0
            
        ## Actuation signal or percent duty cycle to set the motor.
        duty = self.error*self.K_p
        if duty > max_duty:
            duty = max_duty
        elif duty < -max_duty:
            duty = -max_duty
        return duty
    
    def flag(self):
        '''! 
        Sets returns a true statement if the error lands within the
        specified bounds to stop the controller and move to the next value.
        @return flag returns a true statement if error is within the bounds.
        '''
        if self.error >= -100 and self.error <= 100:
            return True
        
    def set_setpoint(self,setpoint):
        '''!
        Sets the setpoint.
        @param setpoint The new setpoint used for the controller.
        '''
        self.i_set = float(setpoint)
        
    def set_gain(self, gain):
        '''!
        Sets the proportional gain.
        @param gain The new proportional gain used for the controller.
        '''
        self.K_p = float(gain)

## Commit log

2022-02-17 Update BOM
2022-02-17 SolidWorks pt. 1
    [Motor.SLDPRT]
2022-02-18 SolidWorks pt.2
    [1346K11_Rotary Shaft.SLDPRT, Flexible Shaft Coupling.SLDPRT, Hex Nut.SLDPRT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]
2022-02-18 SolidWorks pt.3
    [.375 Hex Nut.SLDPRT, 0.125 Hex Nut.SLDPRT, 1346K11_Rotary Shaft.SLDPRT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]
2022-02-18 Pencil Holder
    [Pencil Holder.SLDPRT]
2022-02-18 SolidWorks pt. 4
    [2342K165_Permanently Lubricated Ball Bearing.SLDPRT, Base.SLDPRT, Medium Wheel.SLDPRT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]
2022-02-18 SolidWorks pt. 5
    [Plotter.SLDASM]
2022-02-23 2/23 2:45pm
    [.375 Hex Nut.SLDPRT, 0.125 Hex Nut.SLDPRT, Base.SLDPRT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]
2022-02-24 2/23 4:48pm
    [.375 Hex Nut.SLDPRT, .375 Steel Hex Nut.SLDPRT, 0.125 Hex Nut.SLDPRT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]
2022-02-24 Cost Estimate Spreadsheet
    [Cost Estimate.xlsx]
2022-02-24 2/24 11:10am
    [#10 Phillips Screw.SLDPRT, #10 Steel Hex Nut.SLDPRT, Attachment.SLDPRT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]
2022-02-24 Updated cost estimate
    [Cost Estimate.xlsx]
2022-02-25 Cost Estimate Updated
    [Cost Estimate.xlsx]
2022-02-28 2/27 6:46pm
    [Motor Mount Wire Side.SLDPRT, Motor Mount Wire Side.STL, Motor Mount.SLDPRT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]
2022-02-28 New Plotter Assembly and Pencil Holder
    [.375 Steel Hex Nut.SLDPRT, Base.SLDPRT, Cost Estimate.xlsx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]
2022-03-01 SolidWorks Updated
    [Pencil Holder v3.SLDPRT, Pencil Holder.SLDPRT, Solenoid Housing.SLDPRT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]
2022-03-01 STL files 2/28 5:41pm
    [Lead Screw Mount.SLDPRT, Lead Screw Mount.STL, Wheel.SLDPRT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]
2022-03-01 Solidworks Edits
    [Bearing.SLDPRT, Lead Screw Mount.SLDPRT, Track Slider.SLDPRT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]
2022-03-01 2/28 11:30pm
    [Lead Screw Mount.SLDPRT, Seesaw.SLDPRT]
2022-03-01 3/1 12:01am
    [Seesaw.SLDPRT, TrackSliderv2.SLDPRT]
2022-03-01 Cost Estimate and Solidworks Updates
    [Cost Estimate.xlsx, Lead Screw Mount.STL, Pen to Solenoid Connector Model.SLDPRT]
2022-03-02 3/1 7:43 PM
    [Seesaw.SLDPRT, TrackSliderv2.SLDPRT]
2022-03-03 3/3 8:54pm
    [Seesaw.SLDPRT, Seesaw.STL, TrackSliderv2.SLDPRT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]
2022-03-03 Edits for Track Slider
    [T-Slotted Framing Rail.SLDPRT, TrackSliderv3.SLDPRT]
2022-03-04 Several Solidworks updates
    [Limit Switch.SLDPRT, Seesaw.SLDPRT, Seesaw_v1.SLDPRT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]
2022-03-04 Solidworks 3/4 11:37am
    [TrackSliderv4.SLDPRT, TrackSliderv6.SLDPRT]
2022-03-04 Updates Finalized Hopefully?
    [Seesaw_v2.SLDPRT, Seesaw_v2.STL, Seesaw_v3.SLDPRT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]
2022-03-07 3/7 2:52pm
    [T-Slotted Framing Rail.SLDPRT]
2022-03-09 3/8 5:46pm
    [T-Slotted Framing Rail Middle.SLDPRT, T-Slotted Framing Rail Middle.STL, T-Slotted Framing Rail Motor Side.SLDPRT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]
2022-03-14 3/13 11:17pm
    [TrackSliderv2.SLDPRT]
2022-03-15 3/15 1:19am
    [Attachment.SLDPRT, Seesaw_v1.SLDPRT, Solenoid Housing.SLDPRT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]
2022-03-16 3/15 9:29pm
    [Rotary Shaft.SLDPRT]
2022-03-31 Update Cost Estimate
    [Cost Estimate.xlsx]
